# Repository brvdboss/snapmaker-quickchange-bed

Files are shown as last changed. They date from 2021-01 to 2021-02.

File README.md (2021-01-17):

# Snapmaker-quickchange-bed
 Quick change bed for Snapmaker

The snapmaker 3in 1 3D printer has a 3d print function, cnc function and laser function.
Using these 3 features requires mounting of a different toolhead, but also mounting of different toolbeds. This requires 22 screws that need to be loosened, change bed and again reuse 22 screws (actually not all of them are used for the cnc & laser bed, but it feels like 50 screws).  Especially if you're doing it by hand. (Which I do after breaking a few inserts after using a powertool).

A second challenge is that the carriage of the snapmaker isn't necessarily "flat" (and/or parallell to the x-axis). Especially when 3d printing, the bed and carriage warp with the heat of the heated bed which creates additional annoyances.

To combat this problem I wanted to create a system that allows:
* to easily and quickly change the toolbeds
* provides a rigid and flat surface

The basic idea is to:
* use an MDF baseplate with strong magnets
* pre-mount all the toolbeds to another piece of MDF and have it snap on to the magnets
* require the leqst amount of tools possible to change toolbeds.

This idea has been discussed and pitched in the snapmaker forum: https://forum.snapmaker.com/t/idea-for-quick-switch-bed-feedback-requested/13937 and this repository contains the current solution (work in progress).  Different types of connecting the different plates have been discussed, but so far the magnet based solution seems the easiest. Both in usage and to implement.

The main advantages are:
* Easy to change buildplates, no more screwing around
* Rigid & flat surface (the base plat can be milled to be parallel with the x-axis)
* better insulation for the 3d print plate which should reduce heating times and provide a more stable base temperature. Also less heat transfer to the carriage which should reduce the warping, which is also countered by the MDF

The main disadvantages:
* with 18mm thick MDF you lose up to 36mm of travel on the z-axis. the "top plates"could be made with 10mm MDF as well, making it 26mm. 

## Magnets
Different connector types have been discussed (see forum link) but magnets is my current personal preference.  I'm using 4 pot-magnets (25mm) in diameter.  Using these I can lift the entire snapmaker device held into the air by just these magnets. As such, I think it's more than strong enough to keep the bed in place, even when doing cnc work, which puts the most stress on the bed.

To create a durable mount for the magnets a "pot" is 3d printed which fits the magnet snuggly and a "lid" that fits the metal counterdisk. These fit perfectly together to make the beds "snap" (putting the snap in snapmaker :)) together consistently in the same place and to avoid wearing out the mdf quickly. This seems to work reliably up till now.

In the base-board a cutout is foreseen so you can use a screwdriver (or something else that's long and strong enough) to use as a lever to separate the two plates.

## Some remarks
* This is still a work in progress and only limited field testing has been done, but so far I'm confident it works as expected.
* All designs are now made to be compatible with the A350.  Adjustments would be needed for the A250 and A150
* Everything is designed using openscad which results in stl files.  Some more steps are required to create manufacturing files (cnc)
* The goal is that everything can be created on the snapmaker device itself. (apart from the pot magnets obviously)
* If a nice grid is engraved on the cnc wasteboard this project uses all 3 functions of the device :)

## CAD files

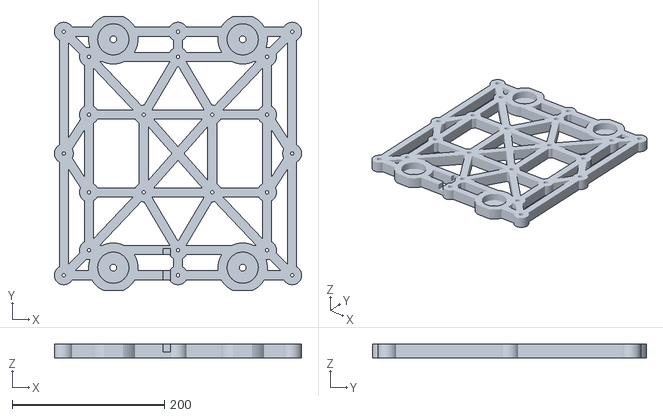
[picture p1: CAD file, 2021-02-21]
stl/bed/bottom-plate_v2.stl
325.0 x 360.0 x 18.0

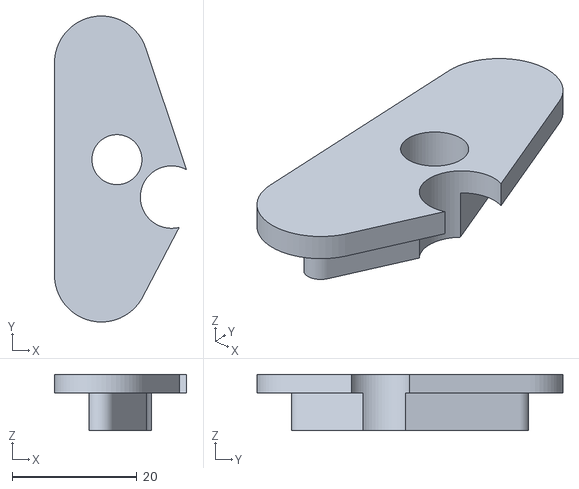
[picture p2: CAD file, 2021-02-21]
stl/connector/magnetholder-embedded.stl
21.1 x 49.0 x 9.00

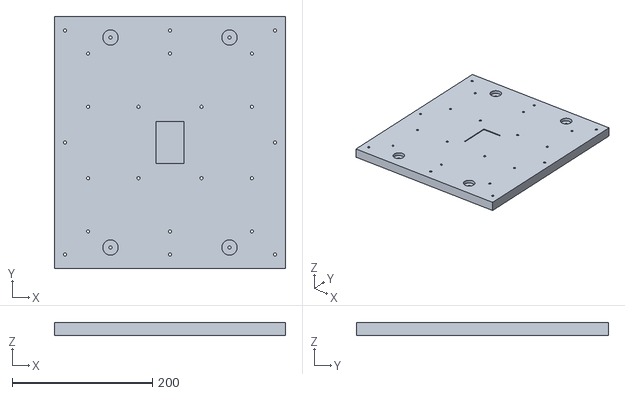
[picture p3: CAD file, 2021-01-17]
stl/bed/3dprint-mountingplate.stl
330.0 x 360.0 x 18.0

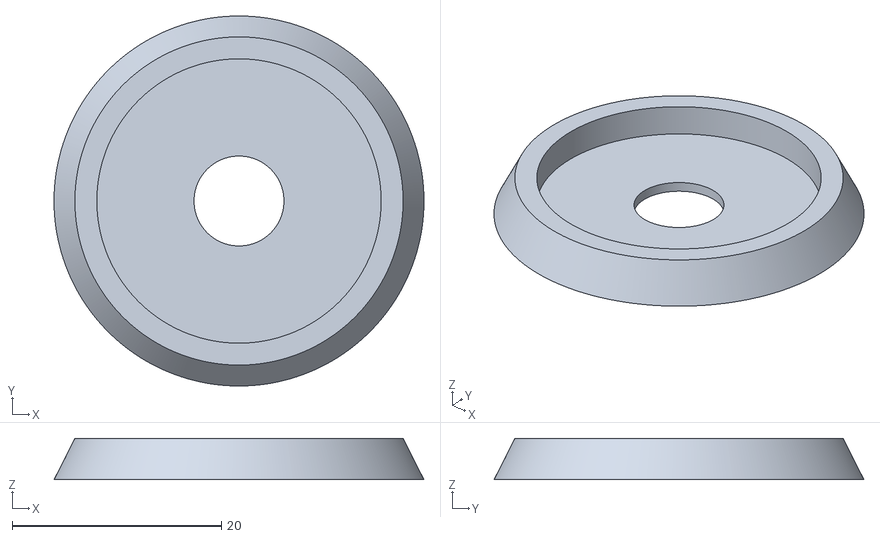
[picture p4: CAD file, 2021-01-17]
stl/connector/magnet-guide-top.stl
35.4 x 35.4 x 3.96

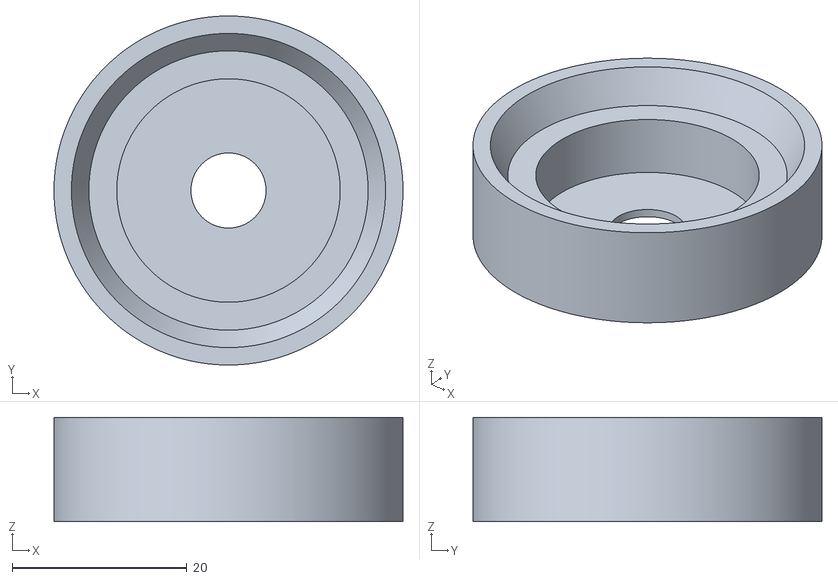
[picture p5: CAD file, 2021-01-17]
stl/connector/magnet-guide-bottom.stl
40.0 x 40.0 x 11.9

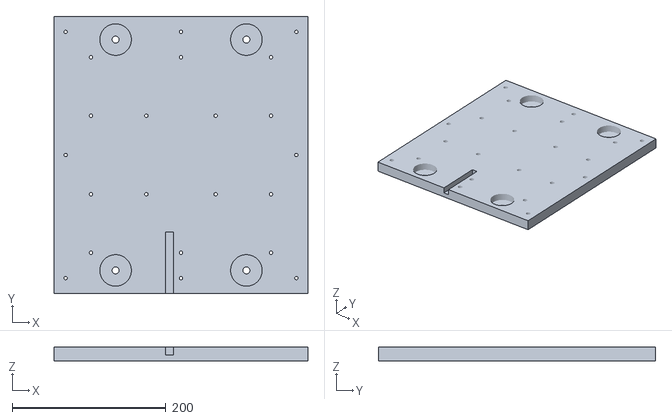
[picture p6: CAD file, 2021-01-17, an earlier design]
stl/bed/bottom-plate.stl
330.0 x 360.0 x 18.0

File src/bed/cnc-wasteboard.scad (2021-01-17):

include <../lib/mountingplates.scad>

cnctopboard();

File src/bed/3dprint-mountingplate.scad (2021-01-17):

include <../lib/mountingplates.scad>

printtopboard();

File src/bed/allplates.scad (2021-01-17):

include <../lib/mountingplates.scad>

translate([boardx/2,boardy/2,750*(1-$t)+boardz*2+boardz/10])
            mountingholes();
translate ([0,0,600*(1-$t)+boardz+boardz/10]) topplate();
//translate ([0,0,450*(1-$t)+boardz]) carriageboltgrid();
translate([0,0,300*(1-$t)+boardz]) printtopboard();
translate([400,0,300*(1-$t)+boardz]) lasertopboard();
translate([400*2,0,300*(1-$t)+boardz]) cnctopboard();
//translate ([0,0,150*(1-$t)+boardz/2]) connectioncrossgrid();
translate ([0,0,0*(1-$t)]) customwasteboard();

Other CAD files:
stl/bed/laser-mountingplate.stl
src/bed/bottom-plate_v2.scad
src/bed/bottom-plate.scad
src/bed/laser-mountingplate.scad
src/connector/magnet-guide-bottom.scad
src/connector/magnet-guide-top.scad

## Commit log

2021-01-17 Initial commit of the project
    First commit after discussion on the snapmaker forum and first tests to validate the concept
    [3dprint-mountingplate.scad, 3dprint-mountingplate.stl, allplates.scad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]
2021-01-17 Fix cutout for the thermistor on the 3d heated bed
    cutout depth was changed but not placed correctly on the z-axis
    [3dprint-mountingplate.stl]
2021-02-21 New version of bottom plate with weight reduction
    Adding a new version of the bottom plate that weighs less than a full plate.
    [bottom-plate_v2.scad, bottom-plate_v2.stl, magnetholder-embedded.stl]
2021-02-21 Revert "New version of bottom plate with weight reduction"
    This reverts commit b69c89896703763a91c336246023824270f3aa03.
    [bottom-plate_v2.scad, bottom-plate_v2.stl, magnetholder-embedded.stl]
2021-02-21 Revert "Revert "New version of bottom plate with weight reduction""
    This reverts commit 6960e8c5b7925ccb5fe8cd990fcd010f122d10d1.
    [bottom-plate_v2.scad, bottom-plate_v2.stl, magnetholder-embedded.stl]
2021-02-21 embedded magnetholder
    If I'm committing it anyway lets commit the correct version.
    idea is to puzzle this in the bed carriage and use it to fix the magnet in place.
    [magnetholder-embedded.stl]
